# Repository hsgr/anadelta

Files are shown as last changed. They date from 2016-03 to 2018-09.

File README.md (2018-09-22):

# Anadelta

Anadelta (Greek: ανάδελτα) means inverted delta and is the name for the algebraic symbol of nabla (or del).

This repository includes all source files designed in freecad and roughly based to [kossel designs](https://github.com/jcrocholl/kossel) to built a delta style 3D printer using 20x20 aluminum extrusions and φ10mm smooth rods.

The firmware is [Marlin](https://gitlab.com/zisi/marlin/tree/anadelta-1.1.8)

The [configuration files](https://gitlab.com/zisi/slic3r-configuration/tree/master/anadelta) for slic3r. 

## License

Licensed under the [CERN OHLv1.2](LICENSE).

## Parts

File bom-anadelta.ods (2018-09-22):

Part | Description | Qty | Price Euro per unit | URL
frame_bottom | Printed part | 3 | - | -
frame_top | Printed part | 3 | - | -
carriege | Printed part | 3 | - | -
end_effector | Printed part | 1 | - | https://www.thingiverse.com/thing:1569106
proximity_sensor_holder | Printed part | 1 | - | -
end_stop_holder | Printed part | 3 | - | -
bed_mount | Printed part | 3 | - | -
bed_mount_clip | Printed part | 3 | - | -
heated_bed | Round aluminium D330mm, W2mm | 1 | 15 | -
filament_spool | for filament | 1 | - | -
t-slot20L1020 | Frame | 3 | 4.2 | http://www.cnccat.com/index.php?id=2&productid=111&catid=57&subcatid=&lang=gr
t-slot20L450 | Frame | 9 | 1.9 | http://www.cnccat.com/index.php?id=2&productid=111&catid=57&subcatid=&lang=gr
precision_shaftD10L1000 | for carriege | 6 | 13 | http://grobotronics.com/precision-shaft-d10mm-x-l1000mm.html
rubber_bumpers | for frame | 3 | 2 | -
frame_cover | Plexiglass, to close the 3d printer | 2 |  | -
frame_cover_door | Plexiglass, to close the 3d printer | 1 |  | -
frame_cover_side | Plexiglass, to close the 3d printer | 3 |  | -
frame_support | To support frame_cover parts, Printed part | 6 | - | -
hinge and “door” latch | for plexiglas “door”, Printed part | 2 | - | https://www.thingiverse.com/thing:755496
end_effector_link | 5.0 x 3.5 x 1000mm, carbon fiber tube (round) | 3 | 5 | https://www.heliland.com/catalog/index.php?main_page=product_info&cPath=11_318&products_id=4718
rod_ends | For M4 threaded rod | 12 | 1 | -
linear Ball Bearing, LM10UU | for carriege | 6 | 1.6 | http://grobotronics.com/linear-ball-bearing-10mm-diameter-lm10uu.html
ball Bearing Flanged, F693ZZ | belt tensioner | 6 | 1.4 | http://grobotronics.com/ball-bearing-flanged-f693zz-3mm-bore-8mm-od.html
timing Belt GT2 | 7m | 7 | 4 | http://grobotronics.com/timing-belt-gt2-1m.html
aluminum Pulley GT2 | 16-tooth | 3 | 4.7 | https://www.fixers.gr/mechanical-parts/motion/pulley-16tooth-gt2.html
hobbed Extruder Gear | In-house | 1 | 3.3 | https://www.fixers.gr/mechanical-parts/hotends/hobbed-mk8-gear-3-0mm.html
E3D V6 Metal Only 3mm hotend | In-house | 1 | - | http://e3d-online.com/v6-3mm-Direct-Metal-Only
bowden.fcstd | for extruder retraction mechanism, In-house | 1 | - | - | https://www.thingiverse.com/make:255303
bowdenLeaver.fcstd | for extruder retraction mechanism, In-house | 1 | - | -
air extruder | to reduce the length of PTFE tube | 1 | - | https://www.thingiverse.com/thing:1259941
rakor | ID 6mm for PTFE, OD M5 | 2 | 1.8 | -
PTFE tube | ID=3.18mm OD=6mm | 1 | 0.77 | https://www.fixers.gr/mechanical-parts/hotends/ptfe-tube-6mm-3mm-3-00.html
spring | for extruder mechanism | 1 | 0.3 | http://grobotronics.com/compression-spring-l20mm-7.5mm-od-5mm-id.html
ball bearing 625ZZ | for extruder | 1 | 0.6 | http://grobotronics.com/ball-bearing-624zz-4mm-bore-13mm-od-clone.html
bowden_sping_spacer | to mount spring, In-house | 1 | - | -
silicone tube | to mount air extruder | 3 | 0.6 | http://grobotronics.com/silicone-tube-transparent-2x4mm-per-meter.html
feed_tube_spinner | for filament, Printed part | 1 | - | https://download.lulzbot.com/AO-101/hardware/printed_parts/stl/
feed_tube_holder | for filament, Printed part | 1 | - | https://download.lulzbot.com/AO-101/hardware/printed_parts/stl/
PSU | 12V – 240W | 1 | - | https://en.wikipedia.org/wiki/Power_supply_unit_(computer)
Thermistor NTC 3950 | NTC 3950 | 2 | 1.5 | http://grobotronics.com/theristor-100kohm-with-cable-for-3d-printer.html
Ceramic Cartridge Heater | 12V – 40W | 1 | 3.2 | http://grobotronics.com/reprap-12v-40w-ceramic-cartridge-heater.html
Kapton Flexible heater | (230 x 230)mm | 1 | 23 | https://www.fixers.gr/electronic-parts/heater-kapton-flexible-23x23.html
Arduino Mega | Atmega 2560 | 1 | 20 | https://www.fixers.gr/arduino-mega-2560.html
RAMPS RepRap Shield | V1.4 | 1 | 10 | http://grobotronics.com/ramps-reprap-shield-for-arduino-mega.html
RAMPS Full Graphic Controller Board | 128x64 | 1 | 18 | http://grobotronics.com/ramps-128x64-full-graphic-controller-board.html
Stepper Motor Driver | DRV8825 | 4 | 5 | http://grobotronics.com/drv8825-stepper-motor-driver.html
Stepper Motor | Nema 17, 4.8kg-cm | 4 | 16 | http://grobotronics.com/stepper-motor-42byghw804.html
DC Brushless Fan | for hot end | 3 | 4.5 | http://grobotronics.com/fan-30x30x10mm-12v-maglev-sunon-ha30101v3-a99.html
DC Brushless Fan | for electronics box | 1 | 2.5 | http://grobotronics.com/dc-brushless-fan-50x50x10mm-12v-slide-bearing.html
Switch | for end-stop | 3 | 0.5 | http://grobotronics.com/microswitch-mini-spdt-on-on-with-roller-simulation.html
LJ12A3-4-Z/BX Proximity Sensor | 12mm/4mm | 1 | 5 | https://www.fixers.gr/lj12a3-4-z-bx-inductive-proximity-sensor.html
Electronics Box | for Ramps and LCD, Printed part | 1 | - | -
Wires
Connectors
Fasteners

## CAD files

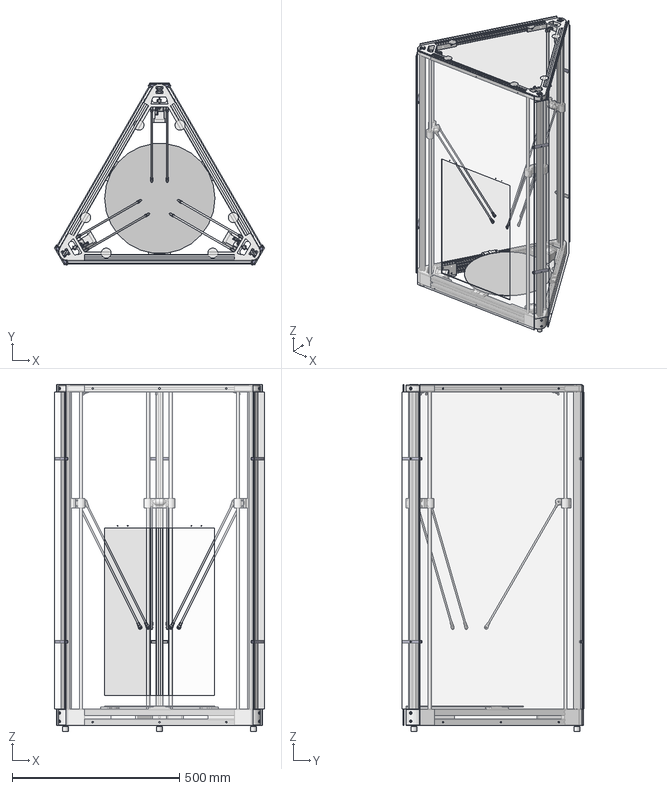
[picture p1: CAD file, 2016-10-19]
anadelta_assembly.fcstd
628.5 x 544.3 x 1038.0 mm
frame_assembly_1_01
frame_assembly_1_02
frame_assembly_1_03
heated_bed_01
frame_cover_01
frame_cover_02
frame_cover_door_01
frame_support_01
frame_support_02
frame_support_03
frame_support_04
frame_support_05
frame_support_06
frame_cover_side_01
frame_cover_side_02
frame_cover_side_03

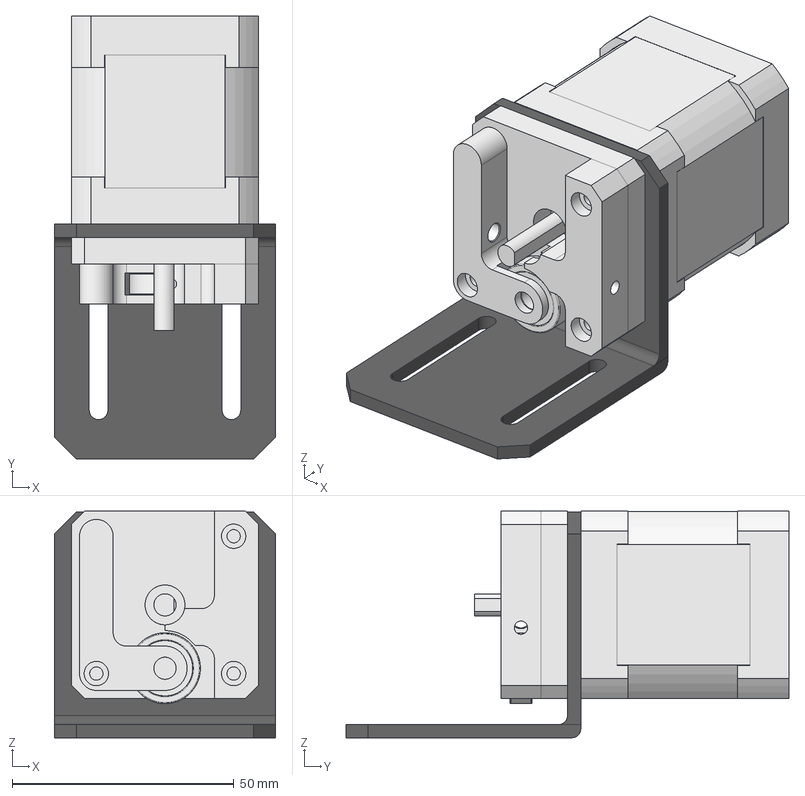
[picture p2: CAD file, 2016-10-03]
extruder/extruder_assembly.fcstd
50.0 x 100.0 x 51.2 mm
motor_mount_01
NEMA_17_Stepper_Motor_47mm_01
bowden_01
bowdenLeaver_01
ball_bearing_625ZZ_01

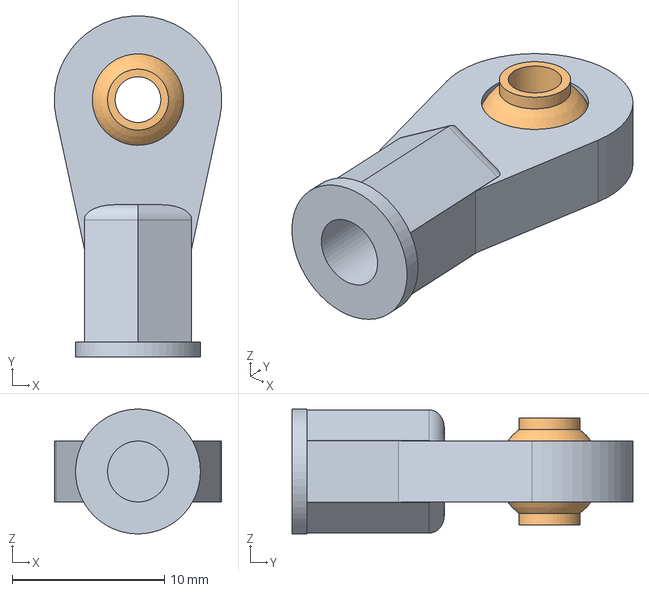
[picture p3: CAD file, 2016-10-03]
shared/rod_end_assembly.fcstd
11.0 x 22.4 x 8.20 mm
rod_end_01
rod_end_ball_01

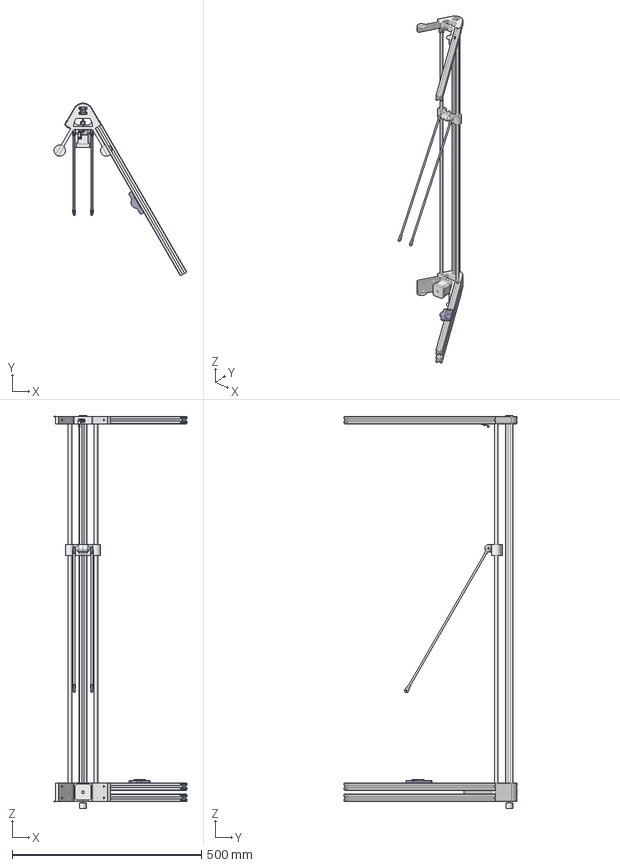
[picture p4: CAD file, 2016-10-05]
frame/frame_assembly_1.fcstd
350.8 x 456.2 x 1038.0 mm
axis_assembly_01
tslot20L450_01
tslot20L450_02
tslot20L450_03
bed_mount_01

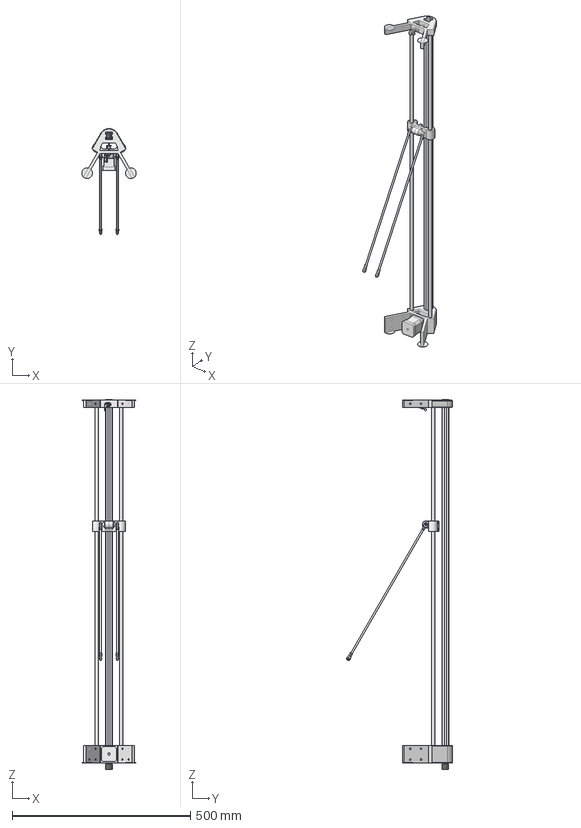
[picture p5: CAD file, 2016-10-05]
frame/axis_assembly.fcstd
152.8 x 297.1 x 1038.0 mm
frame_bottom_01
tslot20L1020_01
NEMA_17_Stepper_Motor_47mm_01
timing_pulley_gt2_16T_01
precision_shaftD10L1000_01
precision_shaftD10L1000_02
carriage_assembly_01
rubber_bumpers__01
frame_top_assembly_01

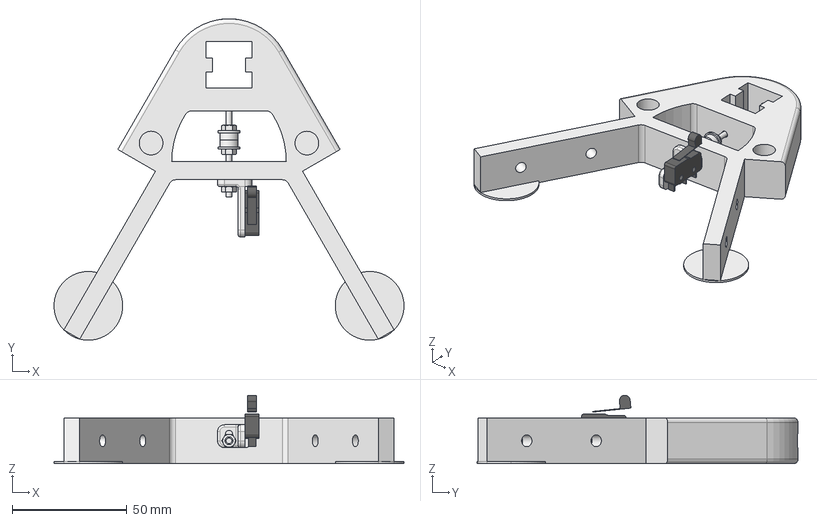
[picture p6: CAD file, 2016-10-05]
frame/frame_top_assembly.fcstd
152.8 x 140.3 x 29.8 mm
frame_top_01
M3_nut_01
threaded_rod_M3L40_01
F693ZZ_ball_bearing_01
F693ZZ_ball_bearing_02
end_stop_holder_01
endstop_01
M3_nut_02
M3_nut_03
M3_nut_04

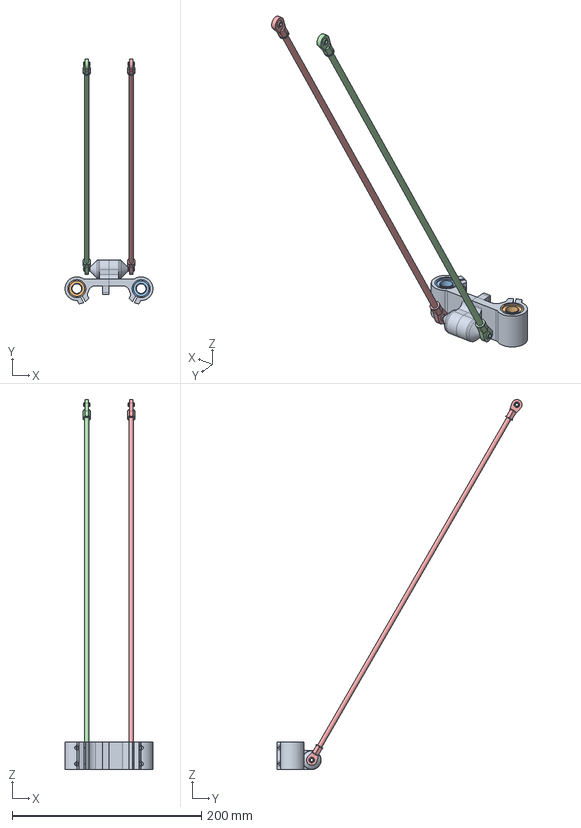
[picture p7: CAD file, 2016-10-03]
frame/carriage_assembly.fcstd
93.0 x 259.2 x 391.2 mm
cariage_01
LM10uu_01
LM10uu_02
end_effector_link_assembly_01
end_effector_link_assembly_02

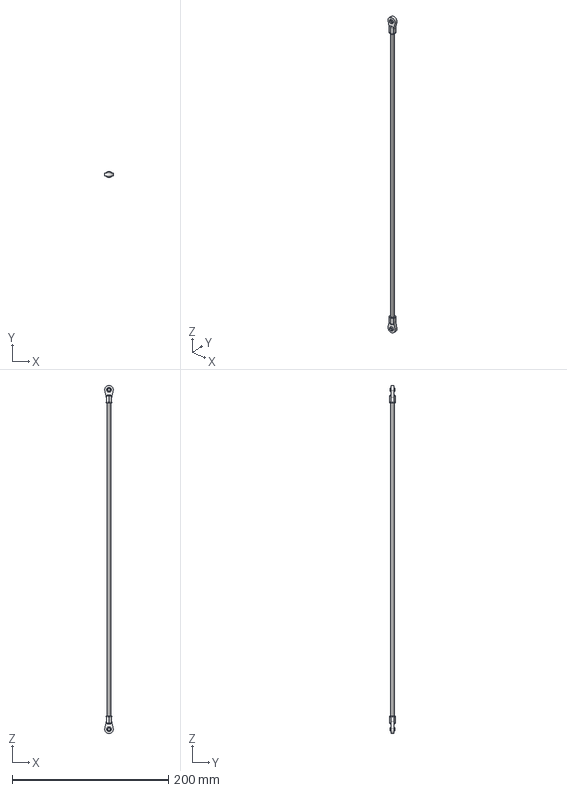
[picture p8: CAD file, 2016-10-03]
frame/end_effector_link_assembly.fcstd
11.0 x 8.20 x 444.8 mm
end_effector_link_01
threaded_rod_M4L15_01
rod_end_assembly_01
threaded_rod_M4L15_01001
rod_end_assembly_02

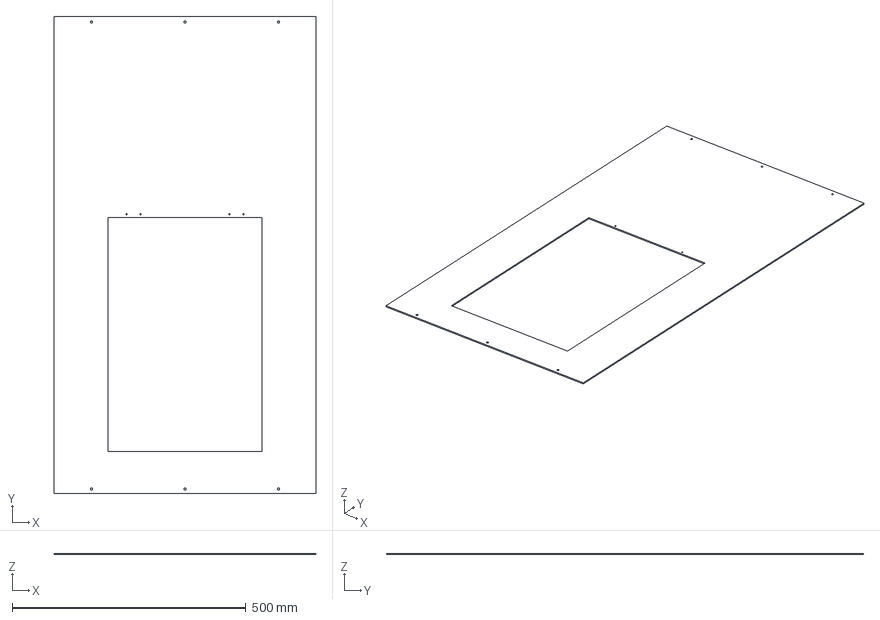
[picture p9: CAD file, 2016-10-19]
frame/frame_cover_door.fcstd
560.0 x 1020.0 x 3.00 mm

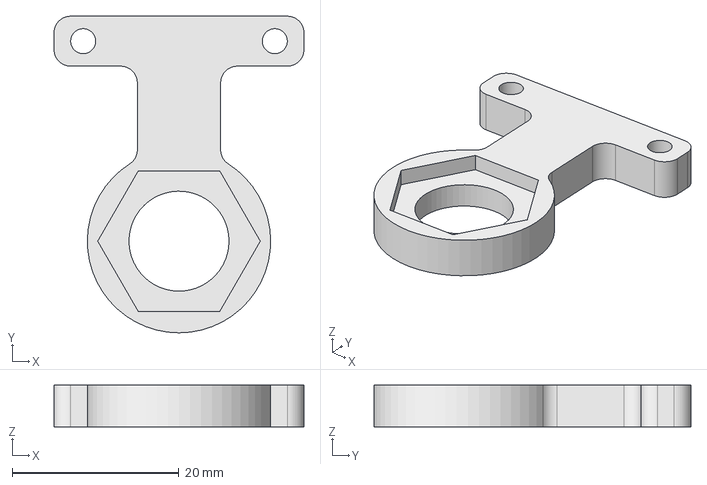
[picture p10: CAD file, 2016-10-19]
hot_end/proximity_sensor_holder.fcstd
30.0 x 38.0 x 5.00 mm

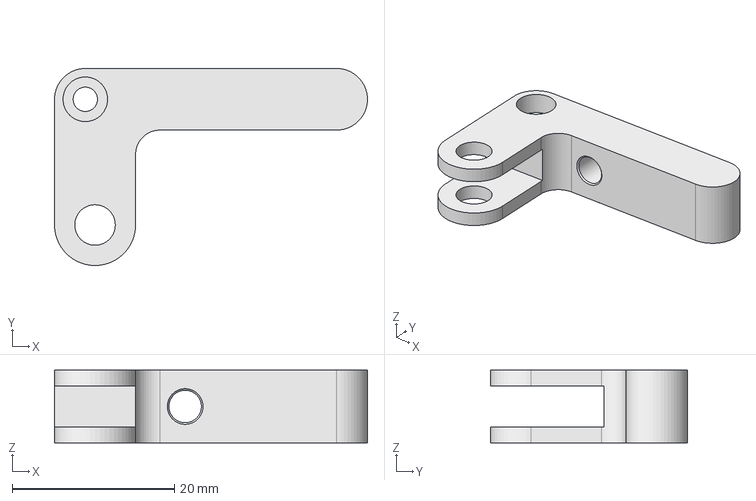
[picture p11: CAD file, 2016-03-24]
extruder/bowdenLeaver.fcstd
38.6 x 24.3 x 9.00 mm

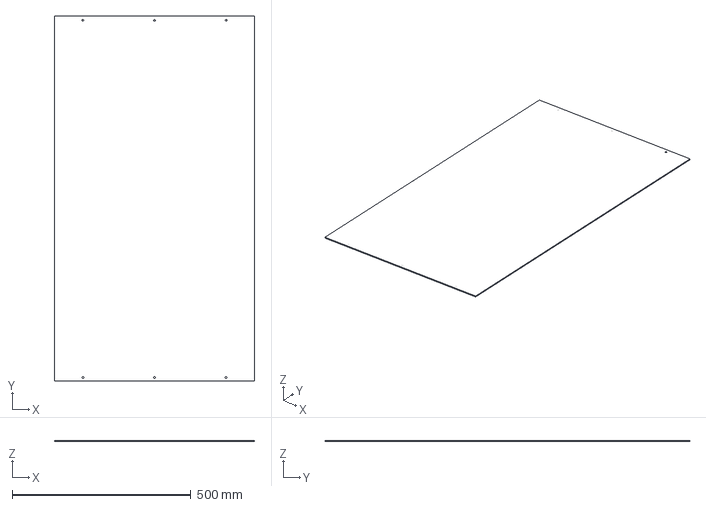
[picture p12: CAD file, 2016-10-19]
frame/frame_cover.fcstd
560.0 x 1020.0 x 3.00 mm

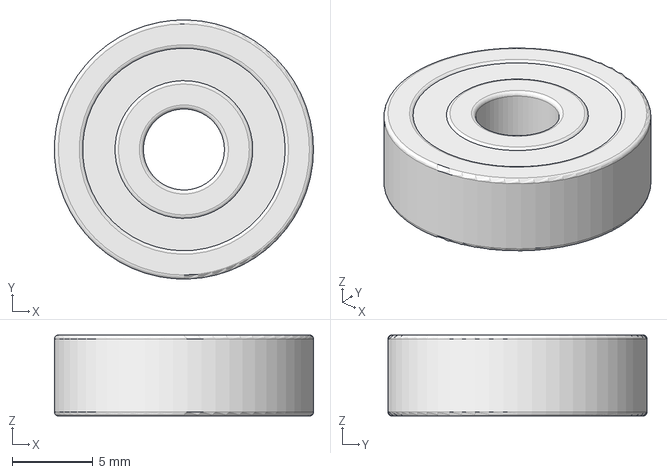
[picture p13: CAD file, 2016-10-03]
shared/ball_bearing_625ZZ.fcstd
16.0 x 16.0 x 5.00 mm

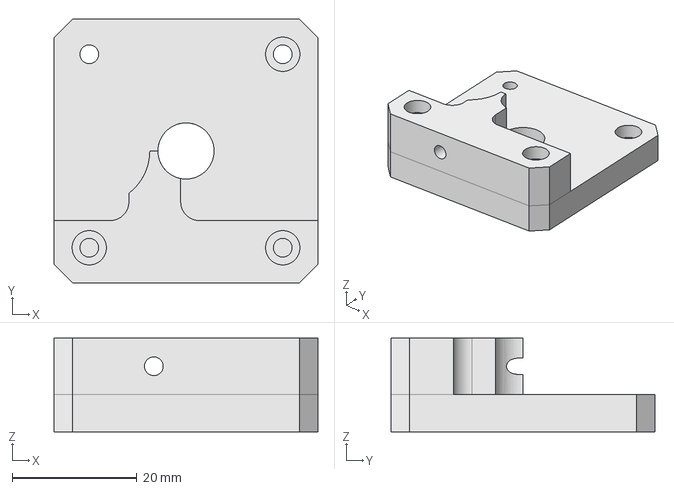
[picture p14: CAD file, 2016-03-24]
extruder/bowden.fcstd
42.3 x 42.3 x 15.0 mm

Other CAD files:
frame/frame_cover_side.fcstd
shared/rubber_bumpers .fcstd
frame/frame_support.fcstd
shared/threaded-rod-M3L40.fcstd
frame/bed_mount.fcstd
frame/bed_mount_clip.fcstd
frame/cariage.fcstd
frame/end_effector_link.fcstd
frame/end_stop_holder.fcstd
frame/frame_bottom.fcstd
frame/frame_top.fcstd
frame/heated_bed.fcstd
frame/tslot20L1020.fcstd
frame/tslot20L450.fcstd
shared/F693ZZ_ball_bearing.fcstd
shared/LM10uu.fcstd
shared/M3_nut.fcstd
shared/NEMA-17_Stepper_Motor_47mm.fcstd
shared/endstop.fcstd
shared/motor_mount.fcstd
shared/precision_shaftD10L1000.fcstd
shared/rod_end.fcstd
shared/rod_end_ball.fcstd
shared/threaded-rod-M4L15.fcstd
shared/timing_pulley_gt2_16T.fcstd

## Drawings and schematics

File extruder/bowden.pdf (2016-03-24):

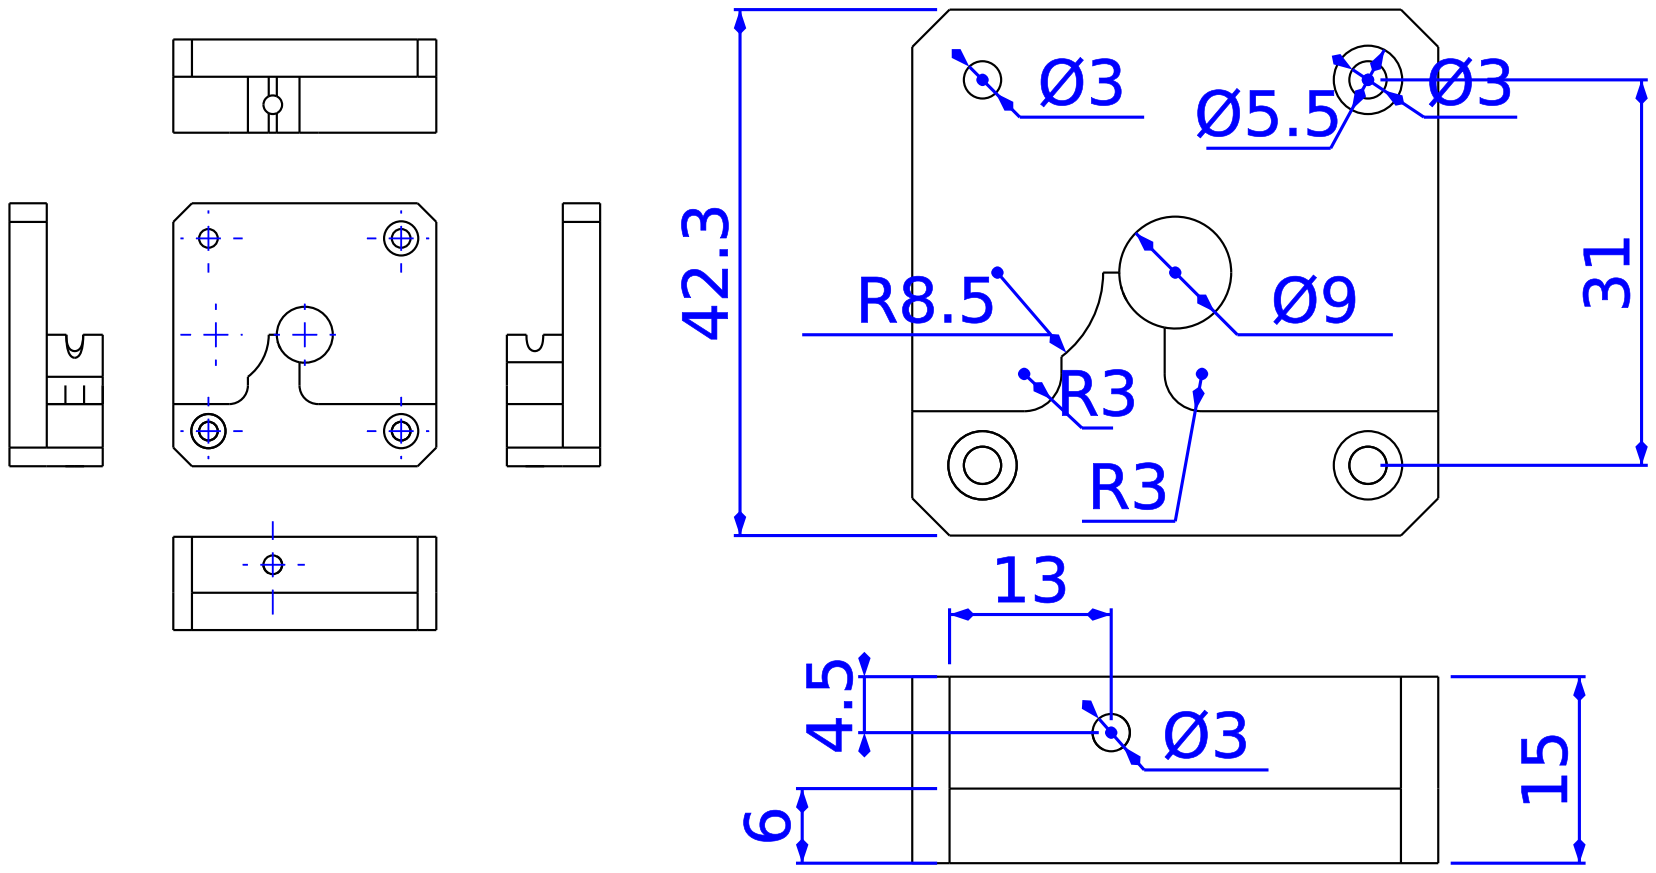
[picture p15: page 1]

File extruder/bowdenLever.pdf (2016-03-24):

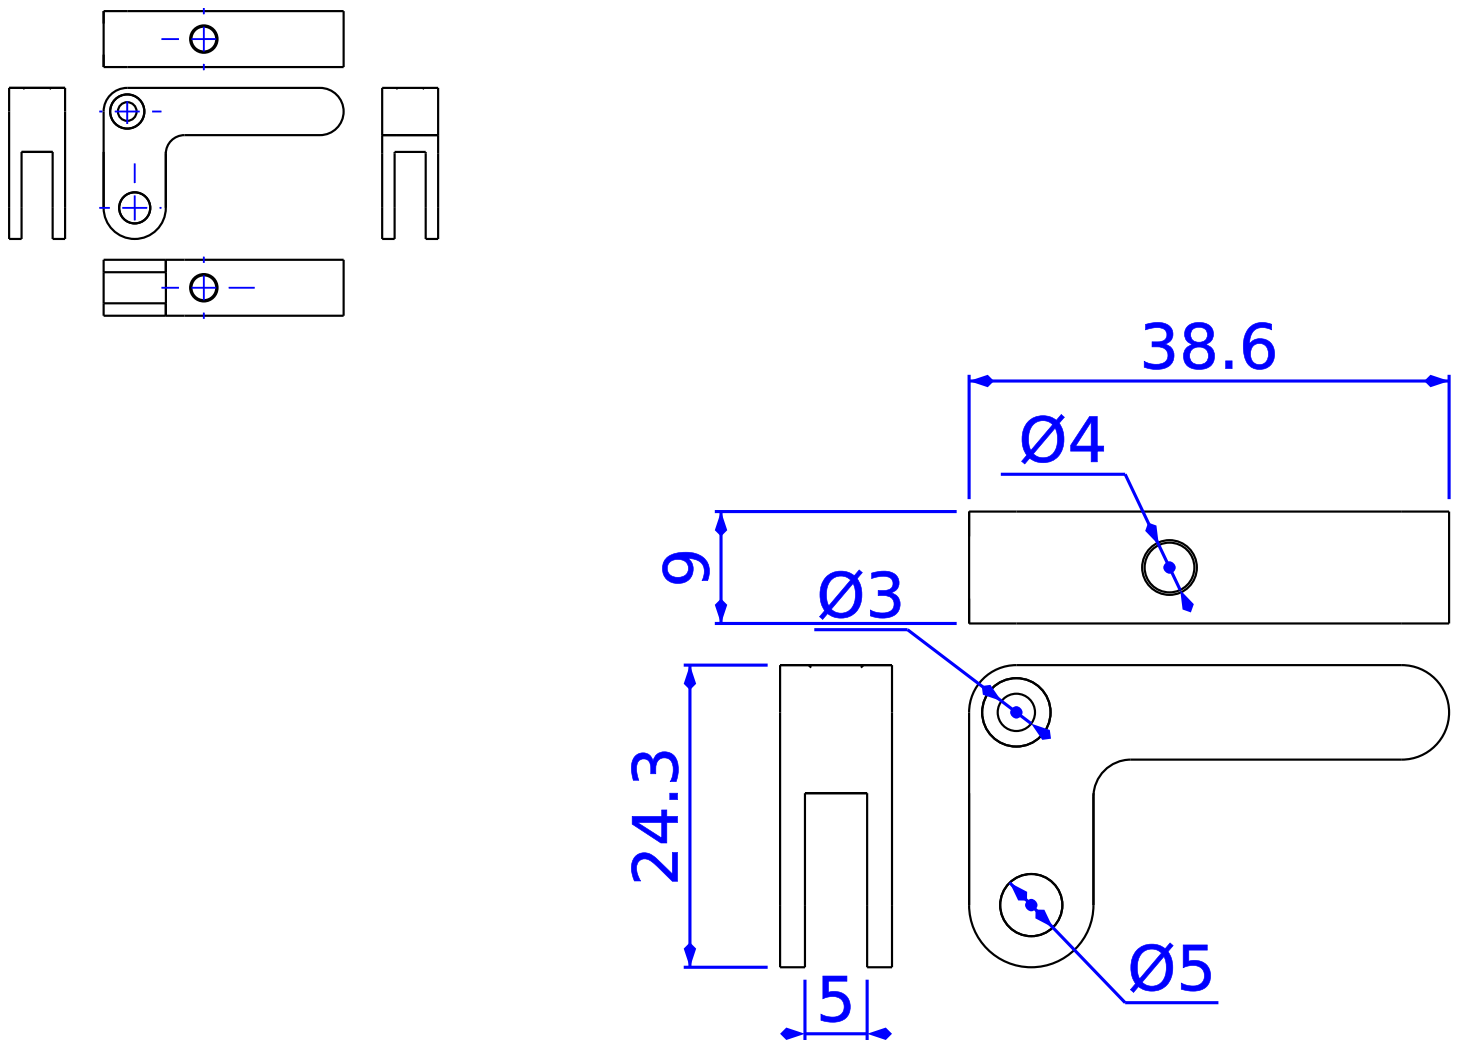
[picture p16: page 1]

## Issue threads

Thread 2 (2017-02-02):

Auto Bed Cooldown after Printing

SotiriosVrachas, 2017-02-02:
After the object was printed the nozzle began the cooldown sequence automatically but the bed stayed hot.

zisi, 2017-02-02:
We can add [M140 S0](http://reprap.org/wiki/G-code#M140:_Set_Bed_Temperature_.28Fast.29) in slic3r [config](https://github.com/hsgr/anadelta/blob/master/config/anadelta_petg_pt2.ini#L18), Printer Settings - Custom G-code - End G-code.

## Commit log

2015-11-13 Initial commit with first two design files and the readme license and gitignore files
    [frame_bottom.fcstd, frame_top.fcstd]
2015-11-14 Add assembly and new parts.
    [anadelta_assembly.fcstd, heated_bed.fcstd, nema17stepper.fcstd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]
2015-11-19 Add cariage part.
    [cariage.fcstd]
2015-12-10 Added firmware configuration
    [Configuration.h, Configuration_adv.h]
2016-03-24 Add latest changes to all files.
    [bowden.fcstd, bowdenLeaver.fcstd, cariage.fcstd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]
2016-03-24 Add fsr mount, update assembly and add BOM.
    [FSR_mount.fcstd, anadelta_assembly.fcstd, bom-anadelta.ods]
2016-03-24 Update configuration file. For using with Marlin-1.1.0-RC4.
    [Configuration.h, Configuration_adv.h]
2016-07-14 Update configuration file.
    [Configuration.h]
2016-10-03 Restructure the files and add new parts.
    [F693ZZ_ball_bearing.fcstd, FSR_mount.fcstd, LM10uu.fcstd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]
2016-10-03 Add common parts for assemblies.
    [M3_nut.fcstd, ball_bearing_625ZZ.fcstd, endstop.fcstd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]
2016-10-03 Update assemblies with new parts.
    [FSR_mount.fcstd, anadelta_assembly.fcstd, axis_assembly.fcstd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]
2016-10-03 Add extruder assembly, WIP.
    [extruder_assembly.fcstd]
2016-10-05 Change the parts of top frame assembly.
    Remove spacer and add M3 nuts to regulate ball bearings.
    Update assemblies and BOM.
    [anadelta_assembly.fcstd, axis_assembly.fcstd, bom-anadelta.ods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]
2016-10-19 Add parts to cover the 3d-printer.
    [anadelta_assembly.fcstd, frame_cover.fcstd, frame_cover_door.fcstd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]
2016-10-19 Add holder for proximity sensor and update BOM.
    [bom-anadelta.ods, proximity_sensor_holder.fcstd]
2016-10-19 Update configuration files for Marlin-1.1.0-RC7.
    Add custom boot-screen, _Bootscreen.h.
    [Configuration.h, Configuration_adv.h]
2016-11-01 Update BOM and configuration files.
    [bom-anadelta.ods]
2016-11-01 Update configuration files.
    Fine tunning of z-probe-offset.
    Enable auto-tunning in bed and tunning PID gains.
    Change the values of preheat temperatures.
    [Configuration.h, Configuration_adv.h]
2018-09-22 Split firmware and configurations in other repos
    [Configuration.h, Configuration_adv.h]
2018-09-22 Add filament tube holder and spinners
    [bom-anadelta.ods]
